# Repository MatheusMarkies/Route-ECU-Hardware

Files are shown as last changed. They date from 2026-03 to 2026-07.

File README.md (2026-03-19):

# DOCUMENTAÇÃO TÉCNICA
## Unidade de Controle Eletrônico (ECU) Automotiva

ECU-Render (https://i.ibb.co/vrg7kG9/ECU-Render.png)

---

**Versão:** 1.5  
**Data:** Setembro 2025  
**Classificação:** Documento Técnico  
**Status:** Em Desenvolvimento  

[Route ECU Firmware](https://github.com/MatheusMarkies/Route-ECU-Firmware)

---

## 1. INFORMAÇÕES GERAIS

### 1.1 Aplicação
ECU destinada ao controle de motores de combustão interna com sistema de injeção eletrônica, com capacidade para:
- 4 cilindros/injetores
- Comunicação CAN bus
- Comunicação Serial
- Armazenamento de dados e mapas

---

## 2. ESPECIFICAÇÕES TÉCNICAS

### 2.1 Especificações Elétricas

| Parâmetro | Mínimo | Típico | Máximo | Unidade |
|---|---|---|---|---|
| Tensão de Entrada | 9 | 12 | 18.81 | V |
| Corrente (Standby) | - | A Determinar | A Determinar | mA |
| Corrente (Operação) | - | A Determinar | A Determinar | mA |
| Corrente por Injetor | - | A Determinar | A Determinar | A |
| Tensão Lógica (MCU) | - | 3.3 | - | V |
| Tensão Periféricos | - | 5.0 | - | V |

Sendo a tensão de perifericos uma tensão derivada do regulador principal, porem com filtros extras para a alimentação de sensores.

### 2.2 Especificações de Gerais

| Característica | Valor | Unidade |
|---|---|---|
| Frequência MCU | 100 | MHz |
| Resolução de Tempo | A Determinar | µs |
| Taxa CAN Bus | A Determinar | kbps |
| Canais de Injeção | 4 | - |
| Canais de Ignição | 4 | - |
| Memória Flash | TBD | KB |
| Memória RAM | TBD | KB |
---

## 3. ARQUITETURA DO HARDWARE

### 3.1 Microcontrolador Principal
- **Família**: STM32H743VIT6 (ARM Cortex-M)
- **Clock Principal**: 16MHz (cristal externo) x2
- **Clock RTC**: 32.768kHz
- **Interfaces**: SPI, I2C, UART, CAN, GPIO

### 3.2 Sistema de Clock
```
Oscilador Principal (16MHz) ──▶ PLL ──▶ System Clock (100MHz)
                                  │
RTC Crystal (32.768kHz) ─────────┴──▶ RTC Clock
```

### 3.3 Mapa de Memória
- **Flash**: Código do programa
- **FRAM**: Dados grandes de acesso rapido
- **SD Card**: Log de dados e Mapas

### 3.4 Sistema de Injeção
- **Atuador**: TIP142
- **Driver**: LM1949 (Modo peak-and-hold)
- **Indicador**: LEDs indicadores individuais para cada canal de injeção

#### 3.4.2 Canais de Injeção
| Canal |
|-------|
| INJ 1 |
| INJ 2 |
| INJ 3 |
| INJ 4 |

INJECTOR (https://i.ibb.co/99wgFJhB/INJECTOR.png)

### 3.5 Sistema de Ignição
- **Atuador**: ISL9V5036P3-F085
- **Driver**: TC4424CPA (Controla duas ignições)
- **Corrente de Pico**: 3A

#### 3.5.2 Canais de Injeção
| Canal |
|------|
| IG 1 |
| IG 2 |
| IG 3 |
| IG 4 |

IGNITION (https://i.ibb.co/ycDnkN8f/IGNITION.png)

### 3.6 Sensores de Posição
- **CKP**: Posição do Virabrequim
- **CMP**: Posição do Comando de Válvulas (Se aplicavel)
- **Tipos de Entradas**: Relutância Variável e Hall
- **Condicionador de Sinal VR**: MAX9924

CKP (https://i.ibb.co/mFYfzqwf/CKP.png)

### 3.7 Sensor MAP
- **Sensor**: MPXA4250AC6U
- **Faixa de Trabalho**: 20 a 250 kPa
- **Relação de Calculo**: VOUT = VCC x (P × 0.004 – 0.04)

MAP (https://i.ibb.co/p6Ym96gr/MAP.png)

### 3.8 Sensor LAMBDA
- **Controlador**: CJ125
- **Controle de Aquecimento**: Sim
- **Sensores**: LSU4.X

LAMBDA (https://i.ibb.co/d0LBV45P/LAMBDA.png)

### 3.9 Sensores Analogicos
- **Conversor das Entradas (map)**: Tensão de Entrada no MCU = 3.205V Quando V_Sensor = 5V

#### 3.9.2 Sensores de Baixa Potencia

| Entrada | Tensão Maxima | TVS | Tipo de Entrada |
|---|---|---|---|
| Entrada 1 | 5V | Sim | Analogico |
| Entrada 2 | 5V | Sim | Analogico |
| Entrada 3 | 5V | Sim | Analogico |
| Entrada 4 | 5V | Sim | Analogico |
| Entrada 5 | 5V | Sim | Analogico |
| Entrada 6 | 5V | Sim | Analogico |
| Entrada 7 | 5V | Sim | Analogico |
| Entrada 8 | 5V | Sim | Analogico |
| Entrada 9 | 5V | Sim | Analogico |
| Entrada 10 | 5V | Sim | Analogico |
| Entrada 11 | 5V | Sim | Analogico |
| Entrada 12 | 5V | Sim | Analogico |

LOW-POWER-SENSOR (https://i.ibb.co/27B8pFJF/LOW-POWER-SENSOR.png)

#### 3.9.3 Sensores de Alta Potencia

| Entrada | Tensão Maxima | Optoacoplada | Tipo de Entrada |
|---|---|---|---|
| Entrada 1 | 12V | Sim | Analogico |
| Entrada 2 | 12V | Sim | Analogico |
| Entrada 3 | 12V | Sim | Analogico |
| Entrada 4 | 12V | Sim | Analogico |

HIGH-POWER-SENSORS (https://i.ibb.co/LzSqFQfp/HIGH-POWER-SENSORS.png)

### 3.10 Saidas

| Entrada | Tensão Maxima | PWM |
|---|---|---|
| Saida 1 | 5V | Sim |
| Saida 2 | 5V | Sim |
| Saida 3 | 5V | Sim |
| Saida 4 | 5V | Sim |

PWM (https://i.ibb.co/xtqXdg2R/PWM.png)

---

## 4. SUBSISTEMAS

### 4.1 Sistema de Alimentação

#### 4.1.1 Conversão DC-DC
- **Entrada**: 12V automotiva (9 a 18.81V)
- **Saídas**: 
  - 5V 2A (periféricos)
  - 3.3V 500mA (MCU e lógica)

## 5. INTERFACES E CONECTORES

### 5.1 Conector Principal (J1)
- **Tipo**: TE 796739-2
- **Função**: Interface principal do veículo
- **Sinais**: Alimentação, CAN, sinais de controle

### 5.2 Headers de Programação

| Designador | Tipo | Função |
|---|---|---|
| J2 | TSM-104-01-L-MT | Debug/SWD |

### 5.3 Interface SD Card (J9)
- **Conector**: 5007620483
- **Protocolo**: SPI
- **Tensão**: 3.3V
- **Capacidade**: Até 32GB

### 5.4 Pinagem do Conector Principal

| Pino | Sinal |
|-----|---|
| **A1** | INJ 1 |
| **A2** | INJ 4 |
| **A3** | INJ 3 |
| **A4** | INJ 2 |
| **B1** | Sensor_In_1 |
| **B2** | CANL |
| **B3** | CANH |
| **B4** | PWM_MCU_OUT_4  |
| **C1** | Sensor_In_2 |
| **C2** | 5V Sensor |
| **C3** | 3.3V |
| **C4** | PWM_MCU_OUT_3  |
| **D1** | Sensor_In_3 |
| **D2** | CMP_IN_1 |
| **D3** | CMP_HALL_IN |
| **D4** | PWM_MCU_OUT_2  |
| **E1** | Sensor_In_4 |
| **E2** | CMP_IN_2 |
| **E3** | GND |
| **E4** | PWM_MCU_OUT |
| **F1** | Sensor_In_5 |
| **F2** | CKP_IN |
| **F3** | CKP_HALL_IN |
| **F4** | CJ125_UP |
| **G1** | Sensor_In_6 |
| **G2** | CKP_IN_1 |
| **G3** | CJ125_IA |
| **G4** | CJ125_UA |
| **H1** | Sensor_In_7 |
| **H2** | Sensor_In_10 |
| **H3** | CJ125_US |
| **H4** | CJ125_IP |
| **J1** | Sensor_In_8 |
| **J2** | Sensor_In_11 |
| **J3** | CJ125_VM |
| **J4** | CJ125_UN |
| **K1** | Sensor_In_9 |
| **K2** | Sensor_In_12 |
| **K3** | MAP_OUT |
| **K4** | Sensor_OPT_3 |
| **L1** | Sensor_OPT_2 |
| **L2** | Sensor_OPT_1 |
| **L3** | Sensor_OPT_0 |
| **L4** | Heater OUT |
| **M1** | Ig 1 |
| **M2** | Ig 2 |
| **M3** | Ig 3 |
| **M4** | Ig 4 |

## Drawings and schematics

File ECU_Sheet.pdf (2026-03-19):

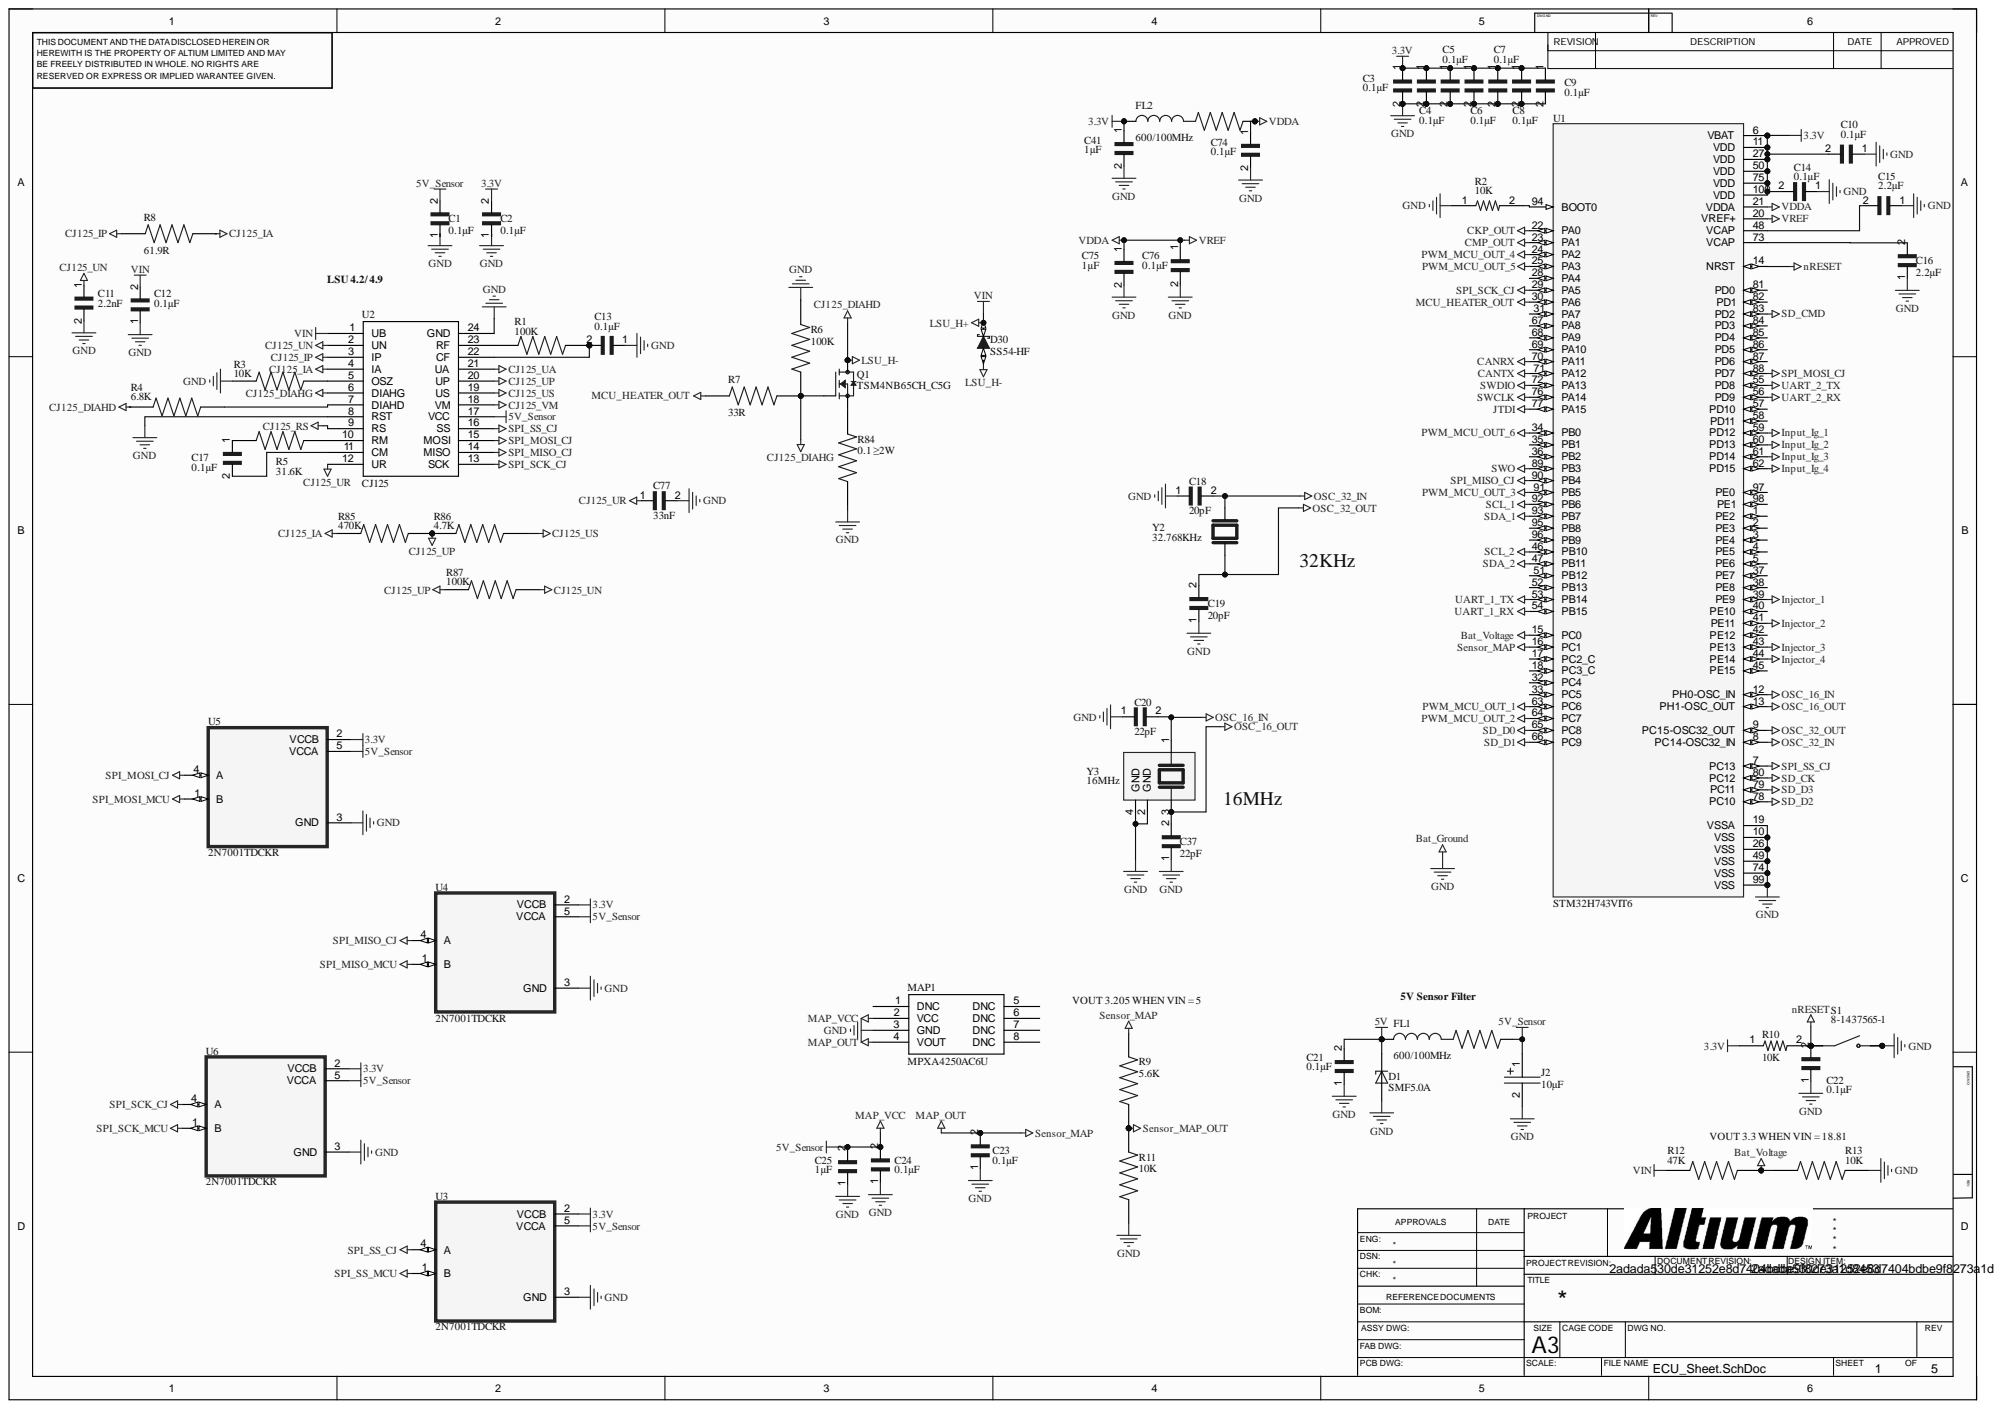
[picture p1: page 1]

1 | 2 | 3 | 4 | 5 | DWG NO: | REV: | 6

THIS DOCUMENT AND THE DATADISCLOSED HEREIN OR HEREWITH IS THE PROPERTY OF ALTIUM LIMITED AND MAY BE FREELY DISTRIBUTED IN WHOLE. NO RIGHTS ARE RESERVED OR EXPRESS OR IMPLIED WARANTEE GIVEN. | 3.3V | REVISION | DESCRIPTION | DATE | APPROVED

ENG: *
CHK: * | | TITLE *

DSN: *

PROJECTREVISION: | DOCUMENTREVISION: | DESIGN ITEM:

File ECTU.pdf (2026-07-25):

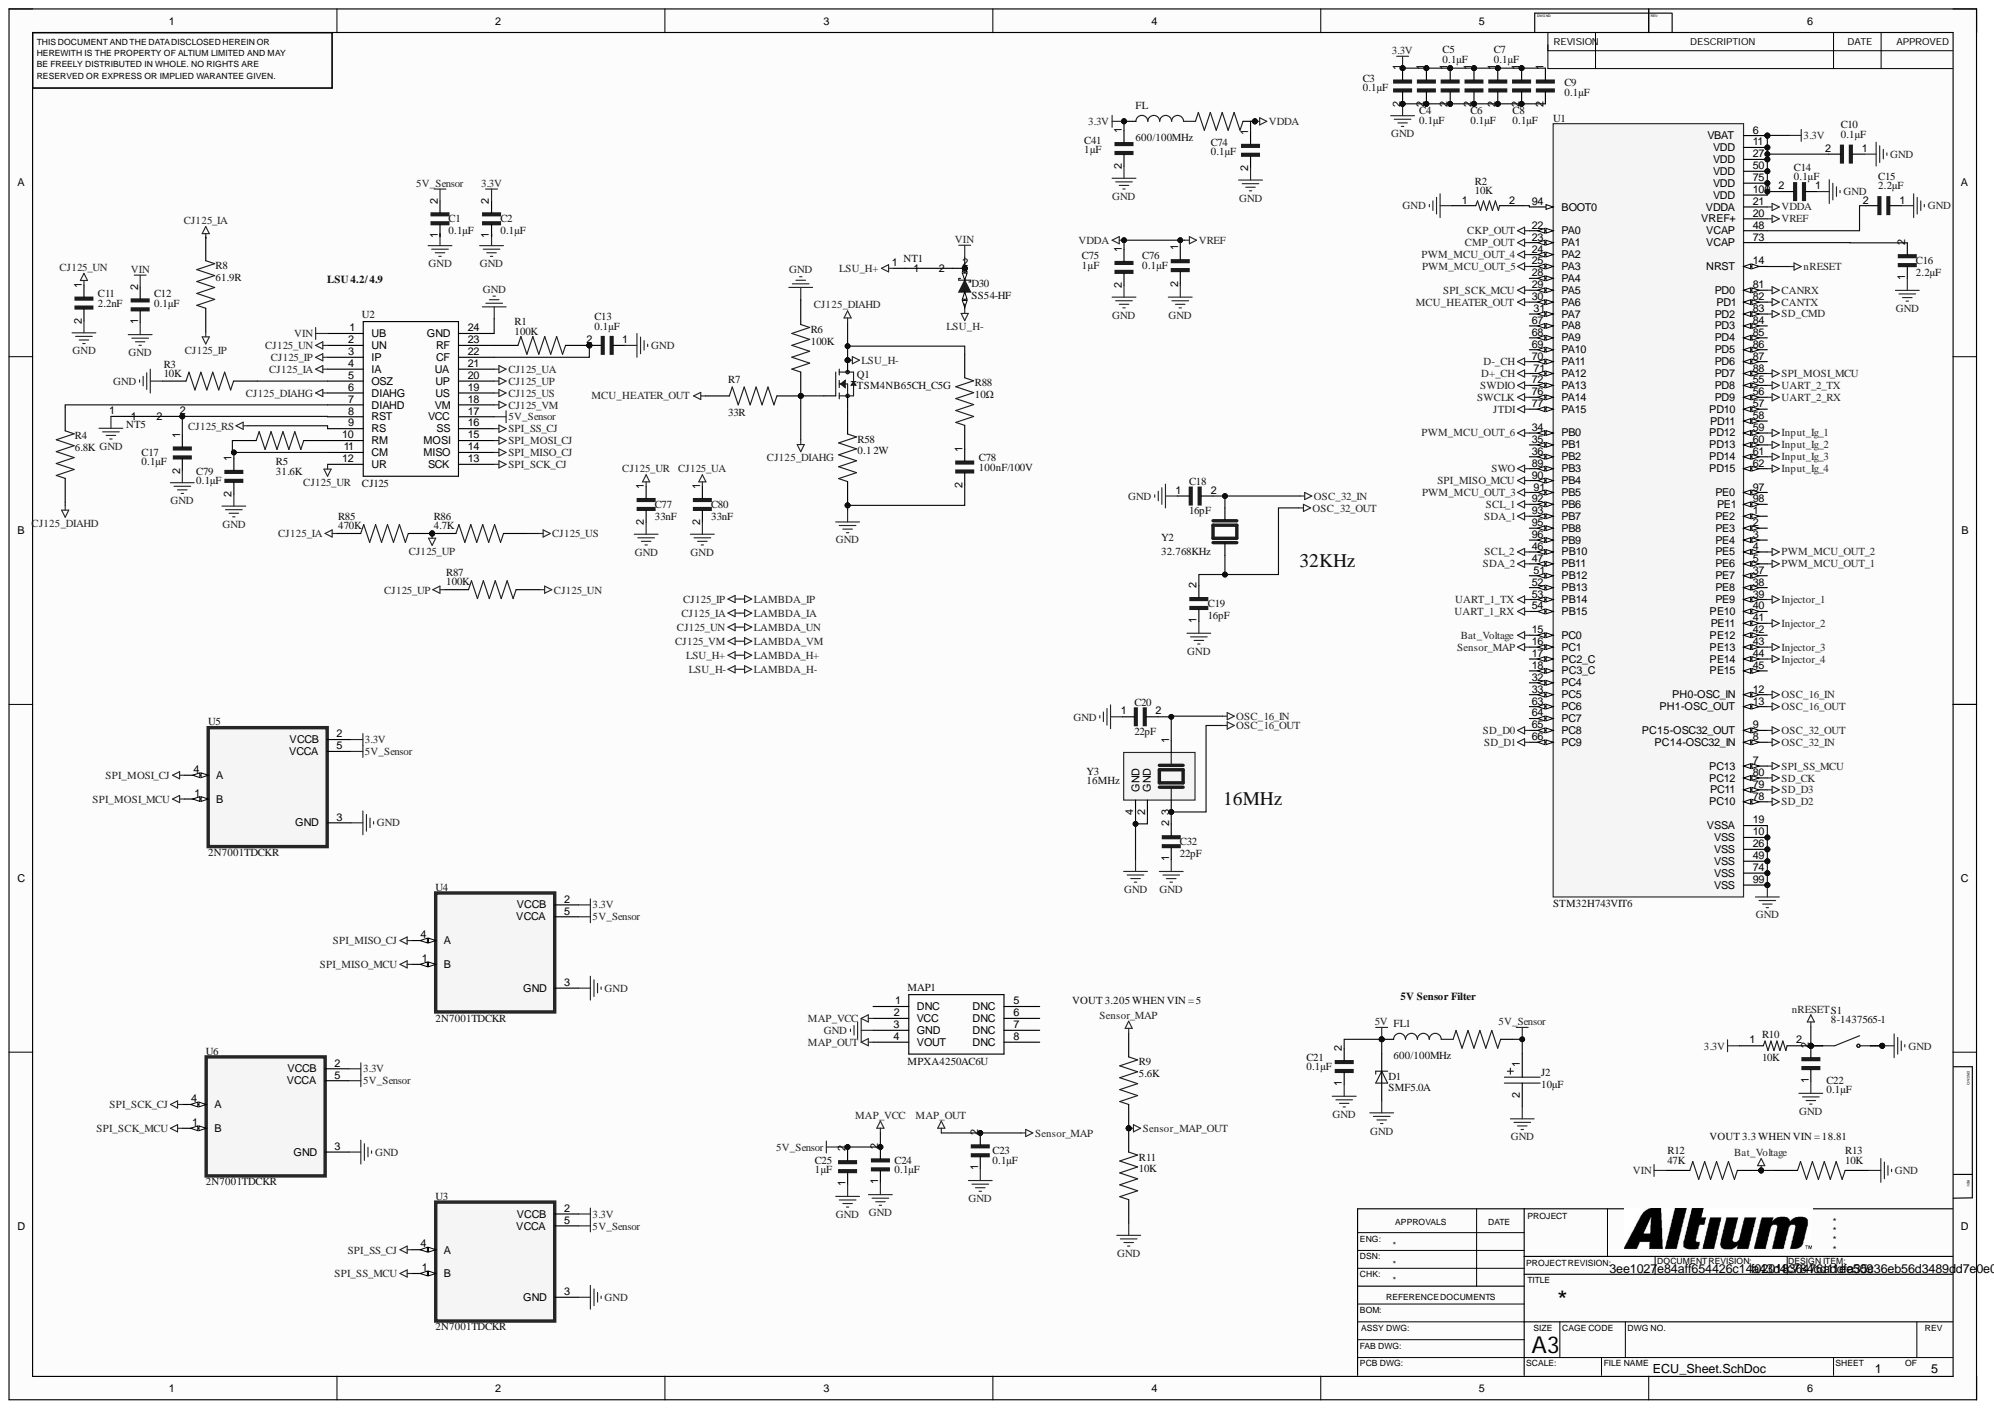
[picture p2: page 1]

DWG NO: | REV:

THIS DOCUMENT AND THE DATADISCLOSED HEREIN OR HEREWITH IS THE PROPERTY OF ALTIUM LIMITED AND MAY BE FREELY DISTRIBUTED IN WHOLE. NO RIGHTS ARE RESERVED OR EXPRESS OR IMPLIED WARANTEE GIVEN. | 3.3V | REVISION | DESCRIPTION | DATE | APPROVED

ENG: *
CHK: * | | TITLE *

DSN: *

PROJECTREVISION: | DOCUMENTREVISION: | DESIGN ITEM:

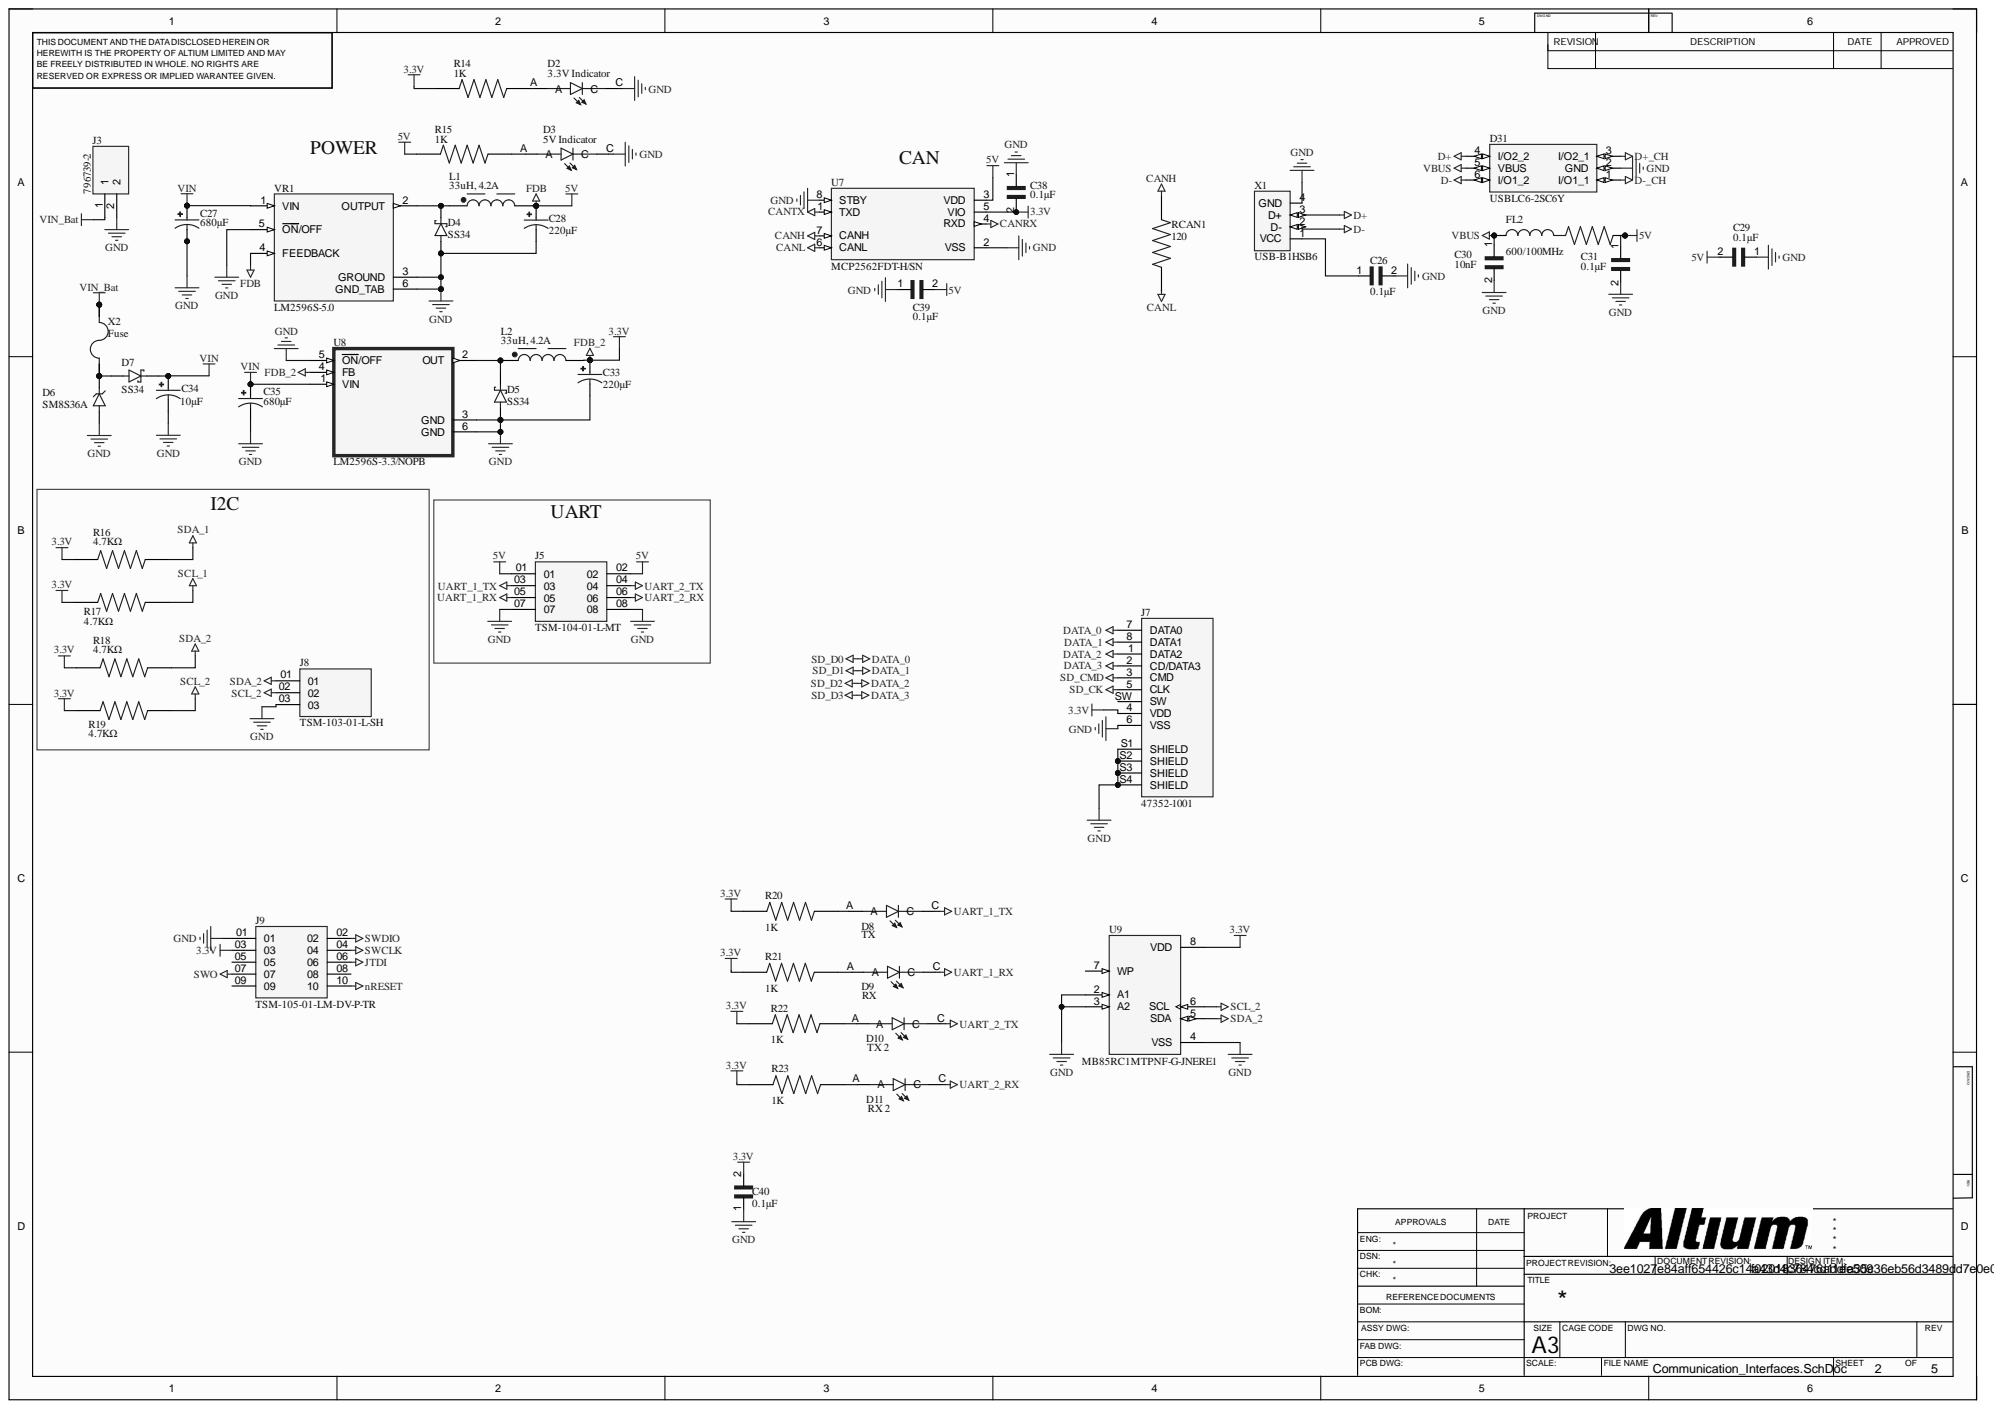
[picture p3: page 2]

TSM-105-01-LM-DV-P-TR

DSN: *

PROJECTREVISION: | DOCUMENTREVISION: | DESIGN ITEM:

CHK: * | | TITLE

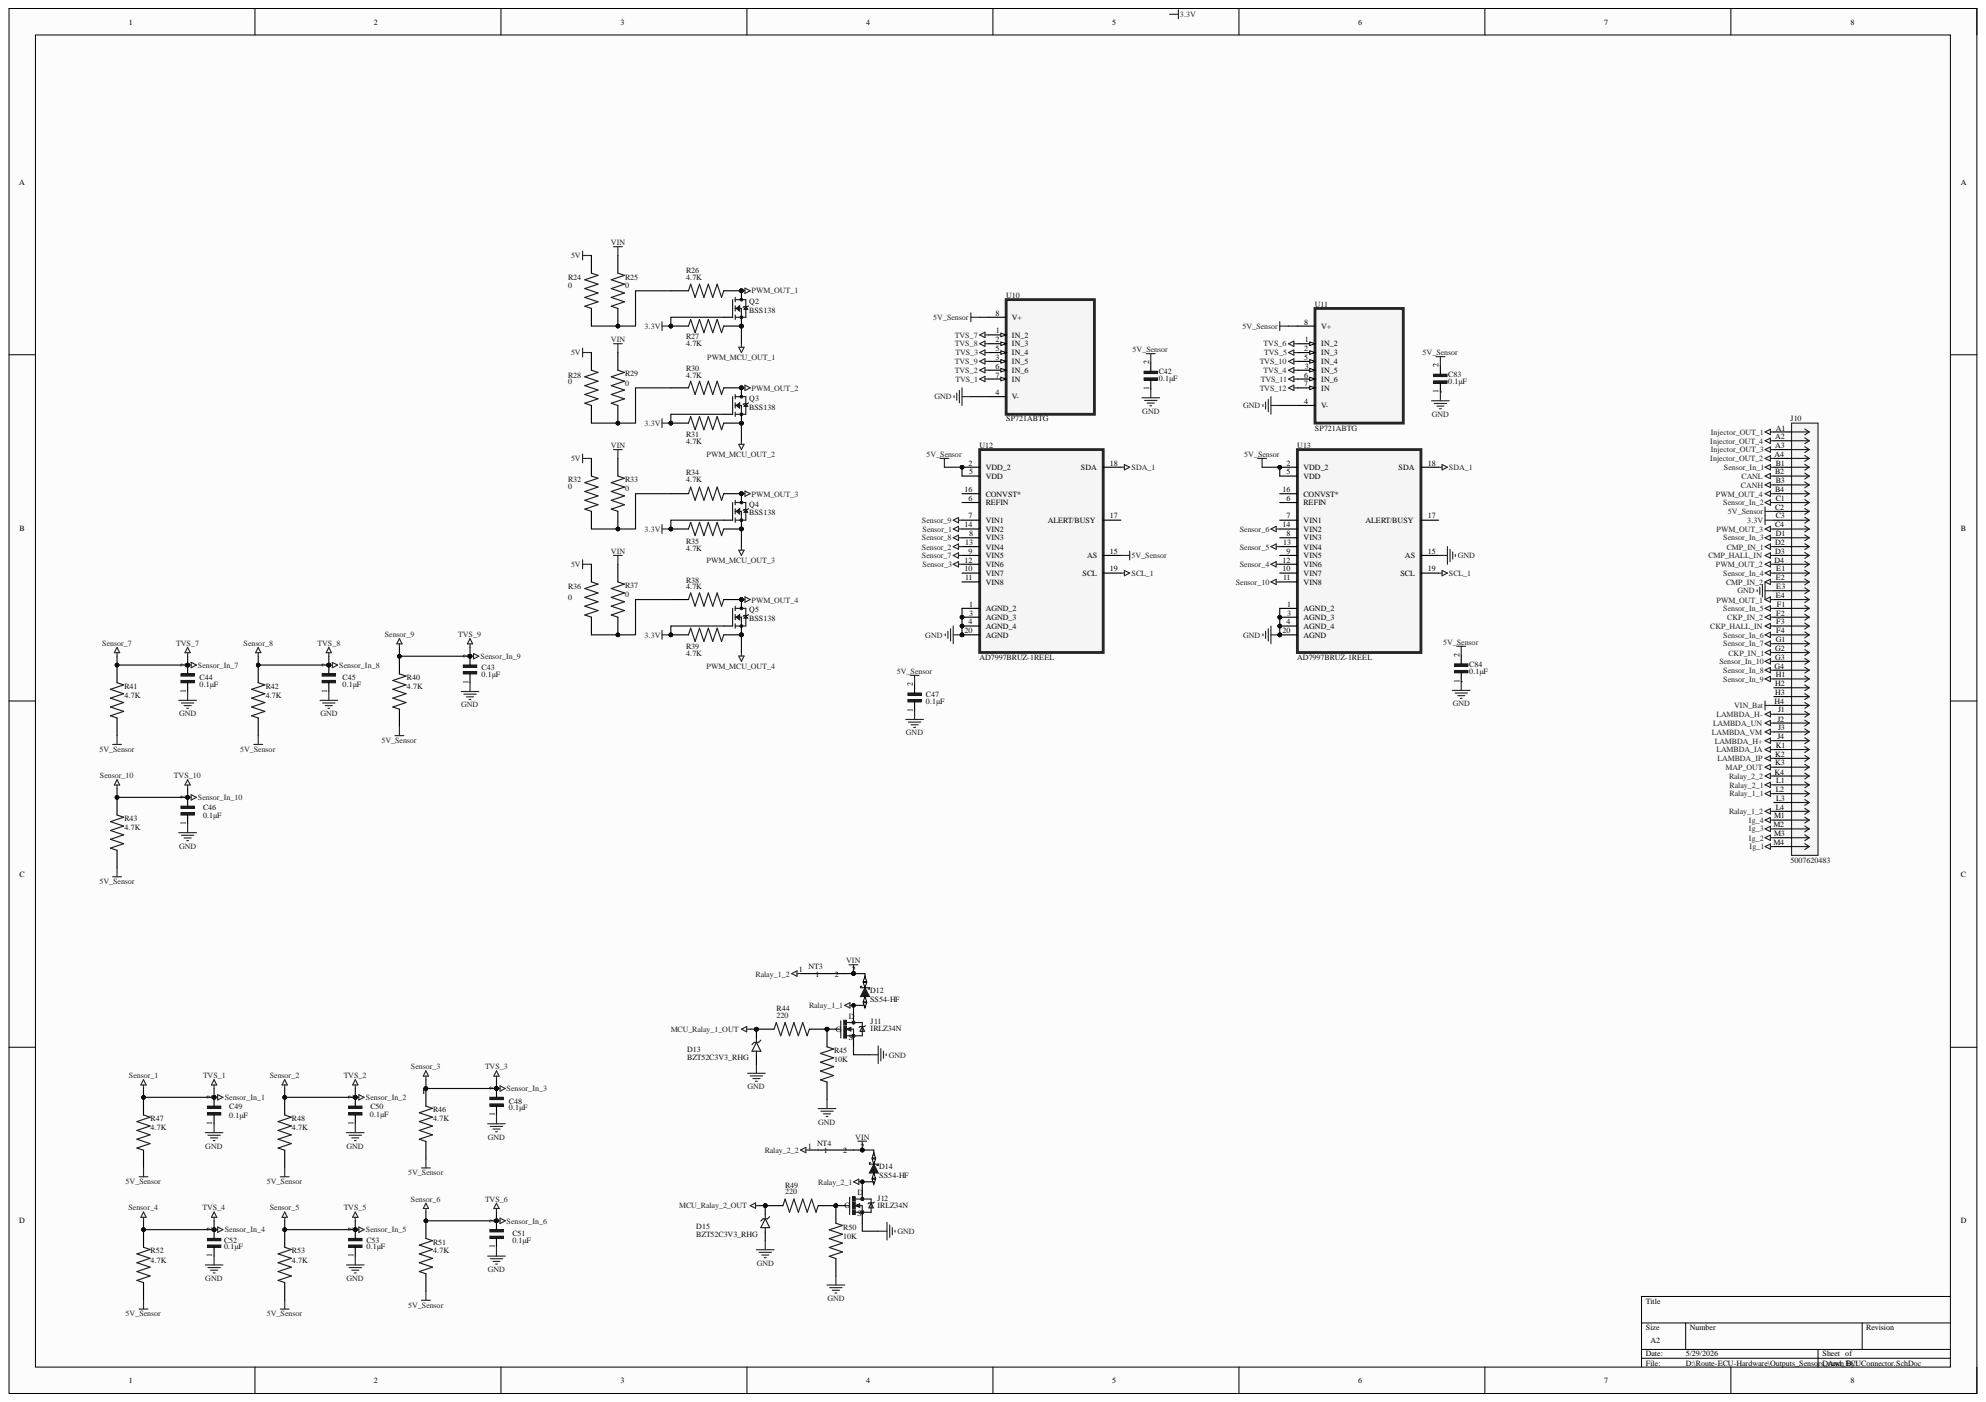
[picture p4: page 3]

sDr _And_E awn BCy:UConne

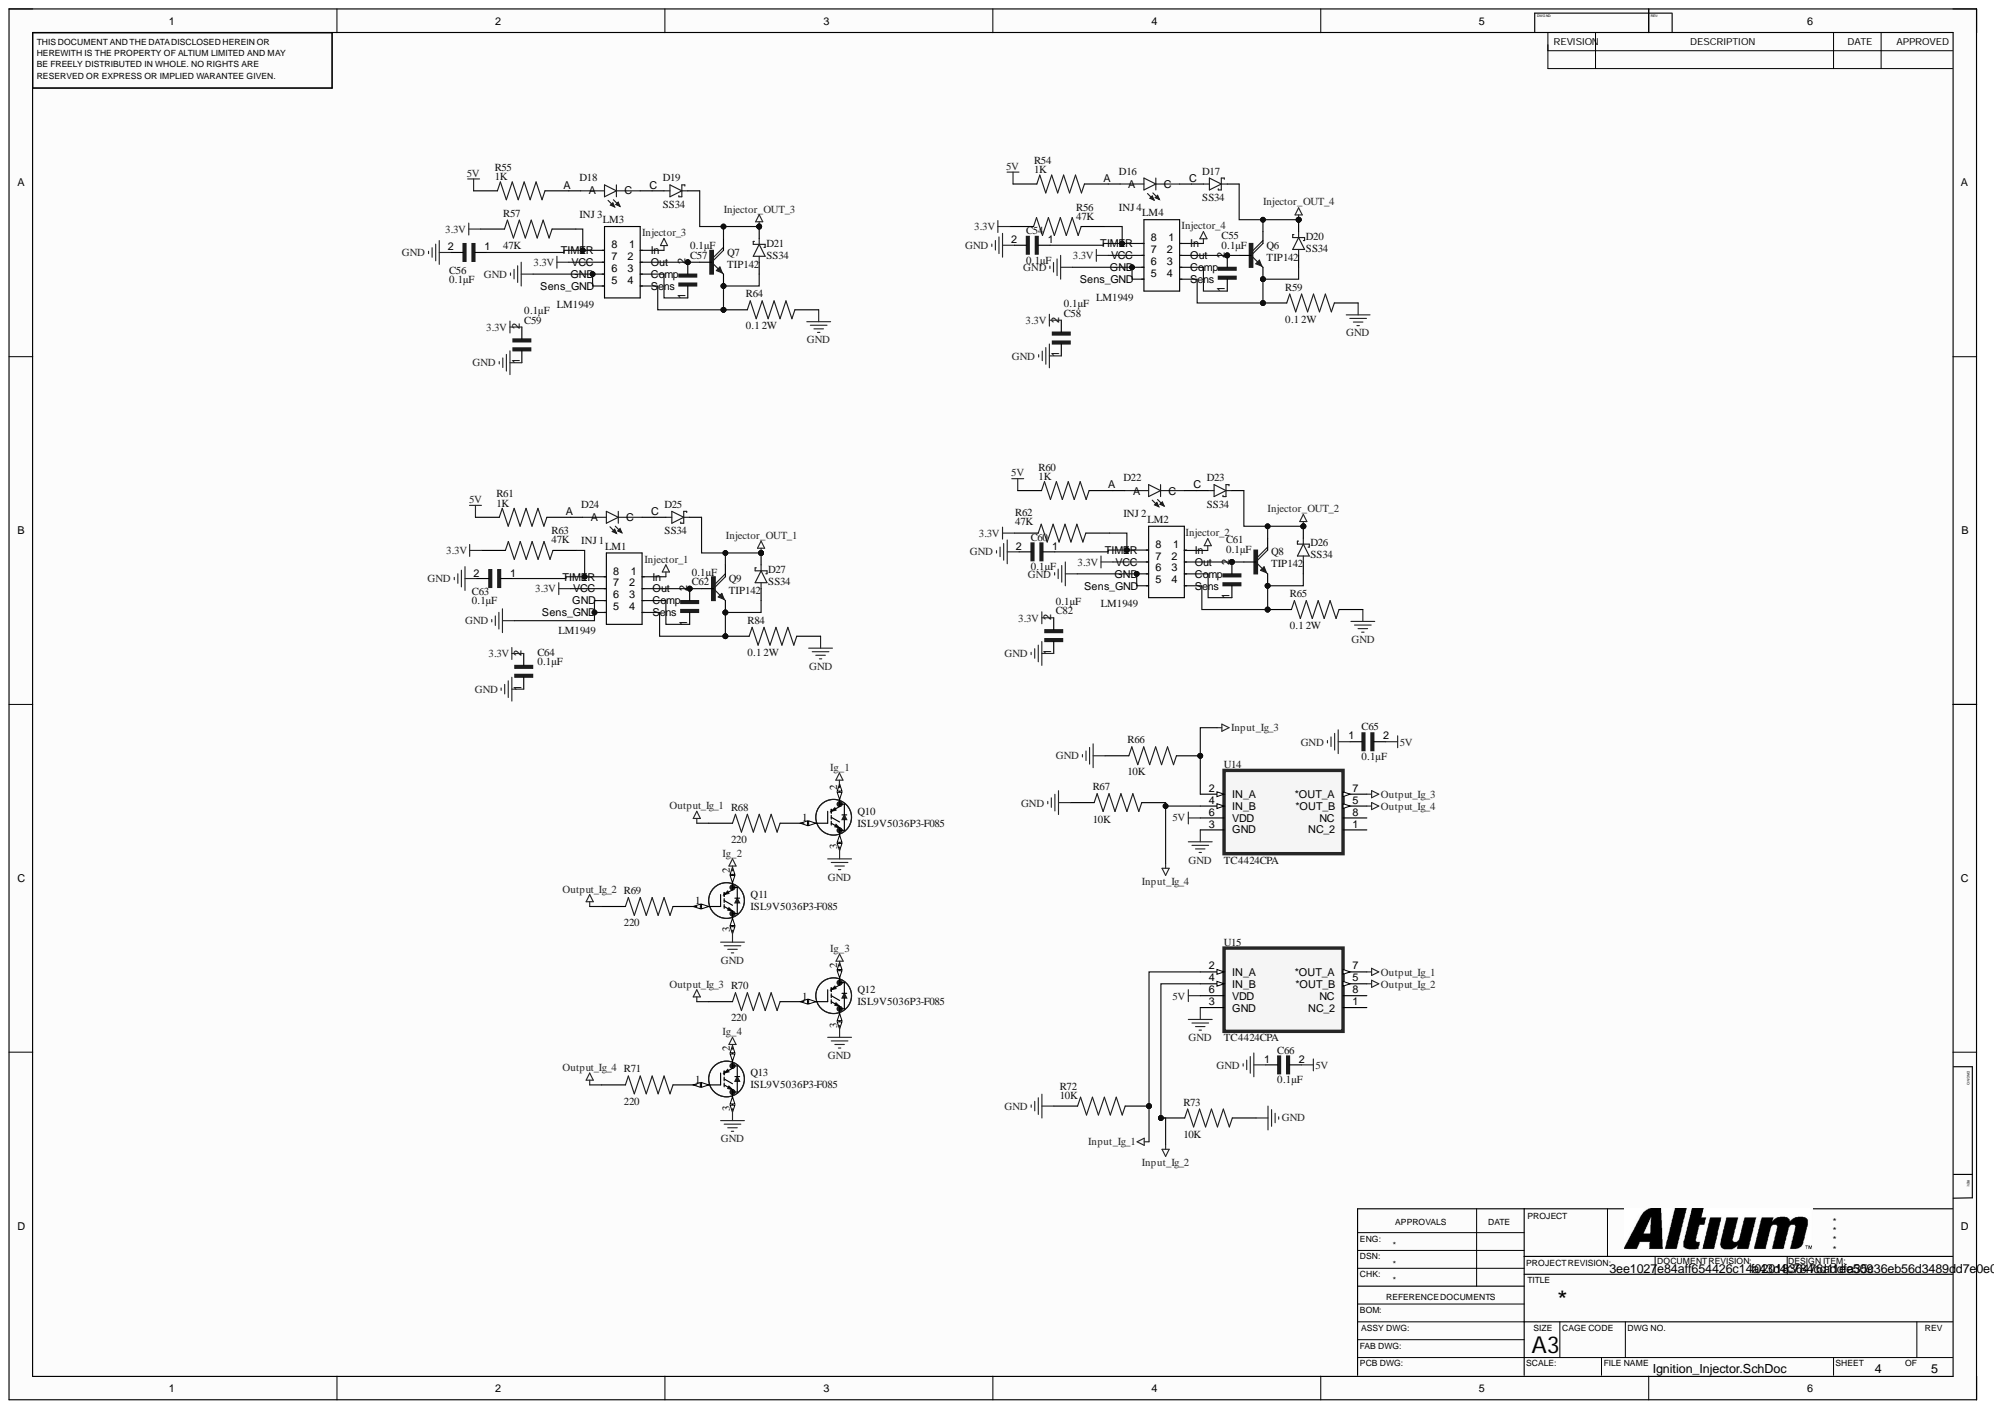
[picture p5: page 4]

Comp 3

DATE | PROJECT | * * APPROVALS * *

ENG: *

DSN: *

PROJECTREVISION: | DOCUMENTREVISION: | DESIGN ITEM:

CHK: * | | TITLE

Ignition_Injector.SchDoc | 4

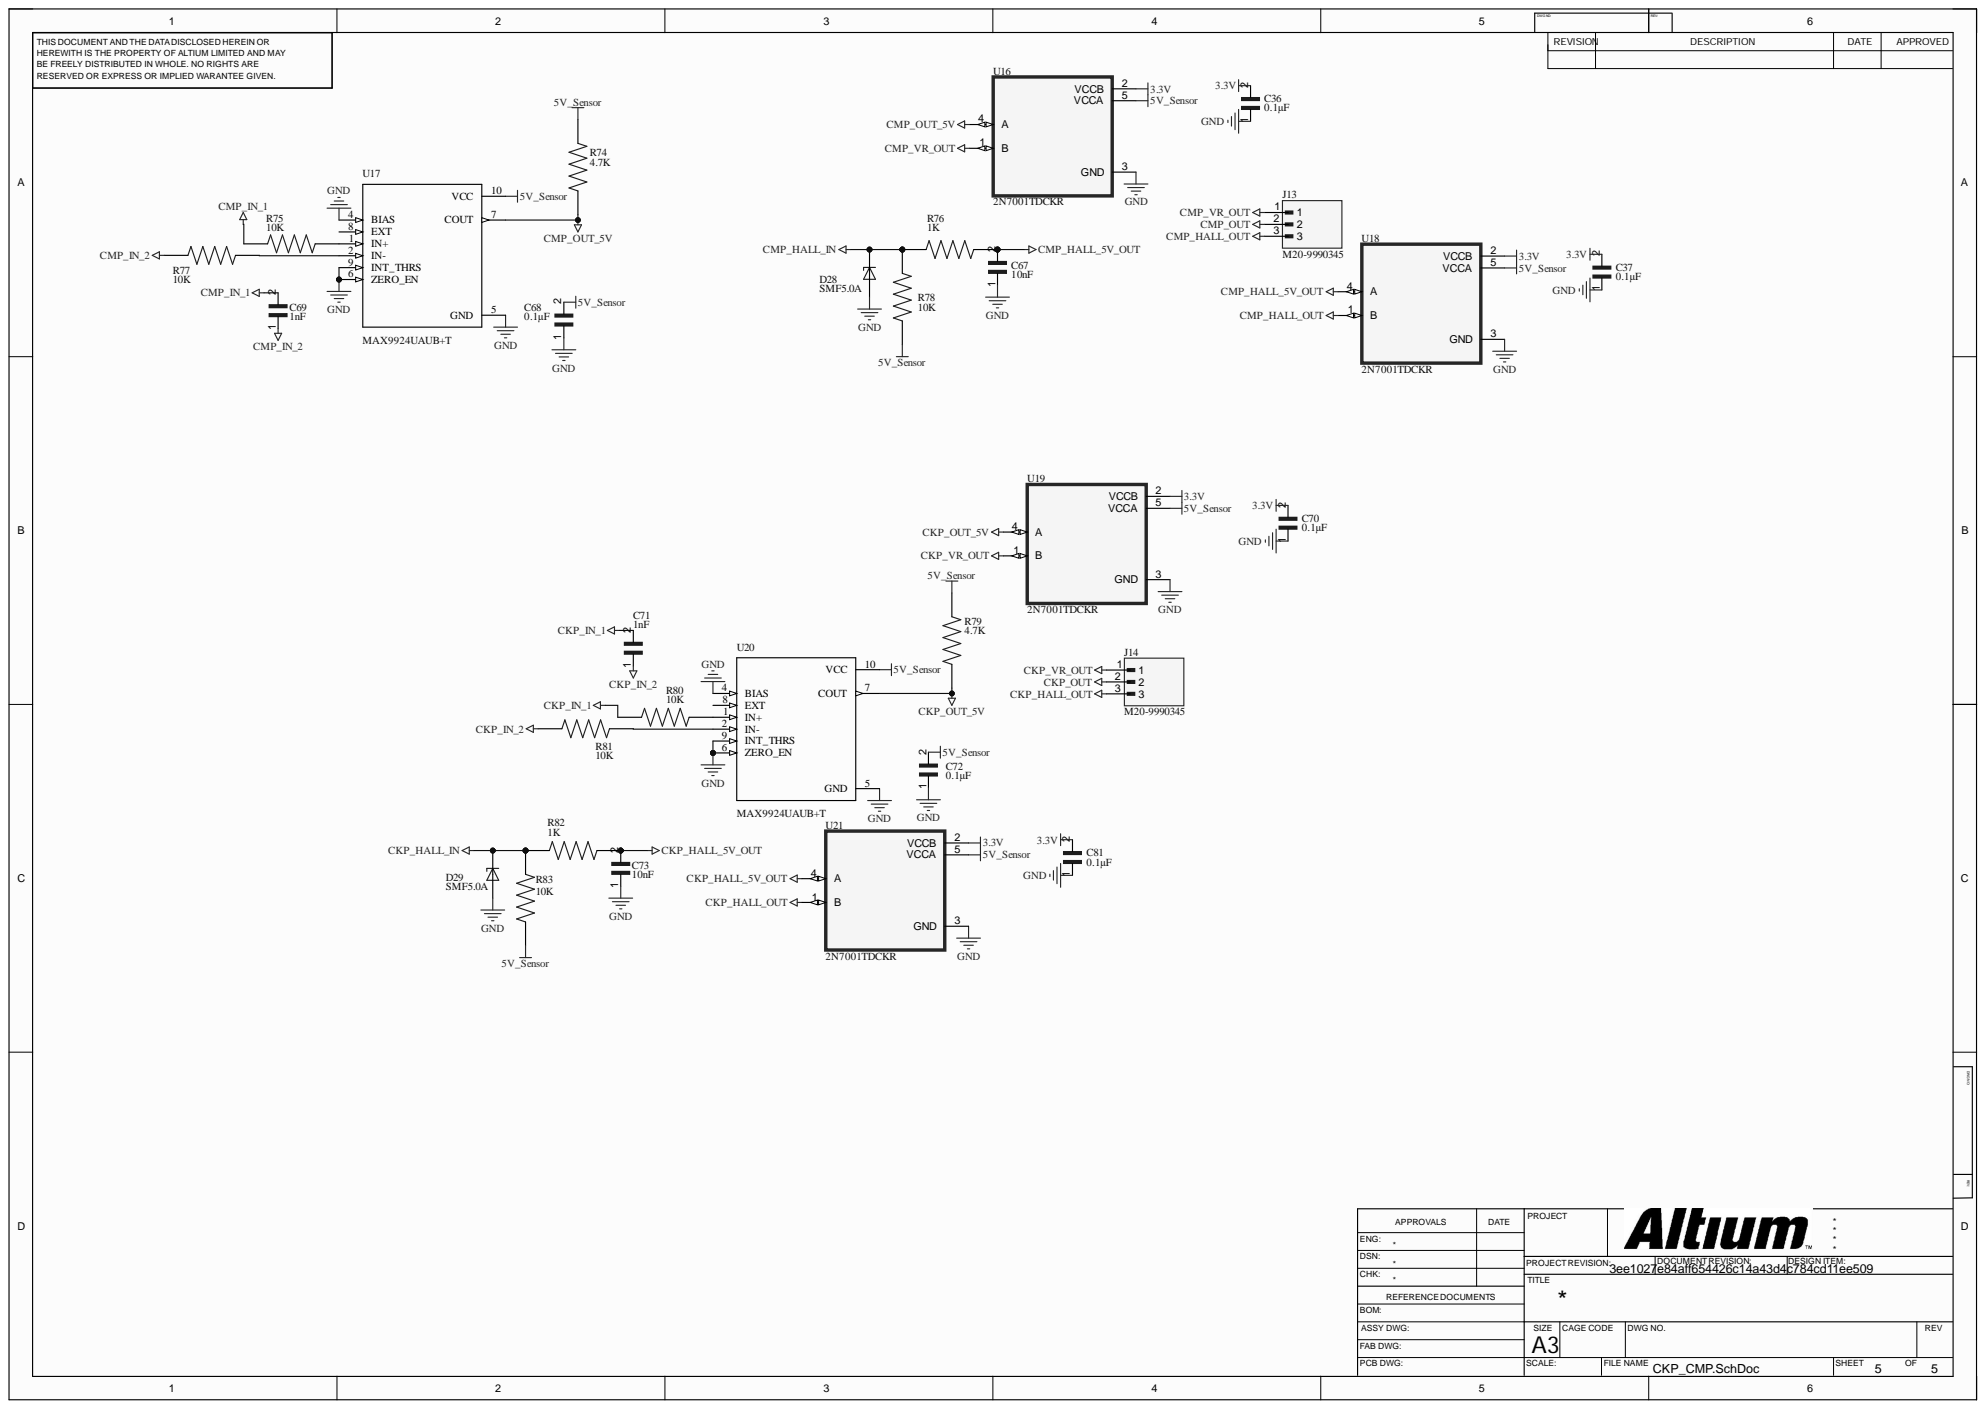
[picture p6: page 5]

DATE | PROJECT | * * APPROVALS * *

ENG: *

DSN: *

PROJECTREVISION: 3ee1027e84aff654426c14a43d4c784cd11ee509 | DOCUMENTREVISION: | DESIGN ITEM:

CHK: * | | TITLE

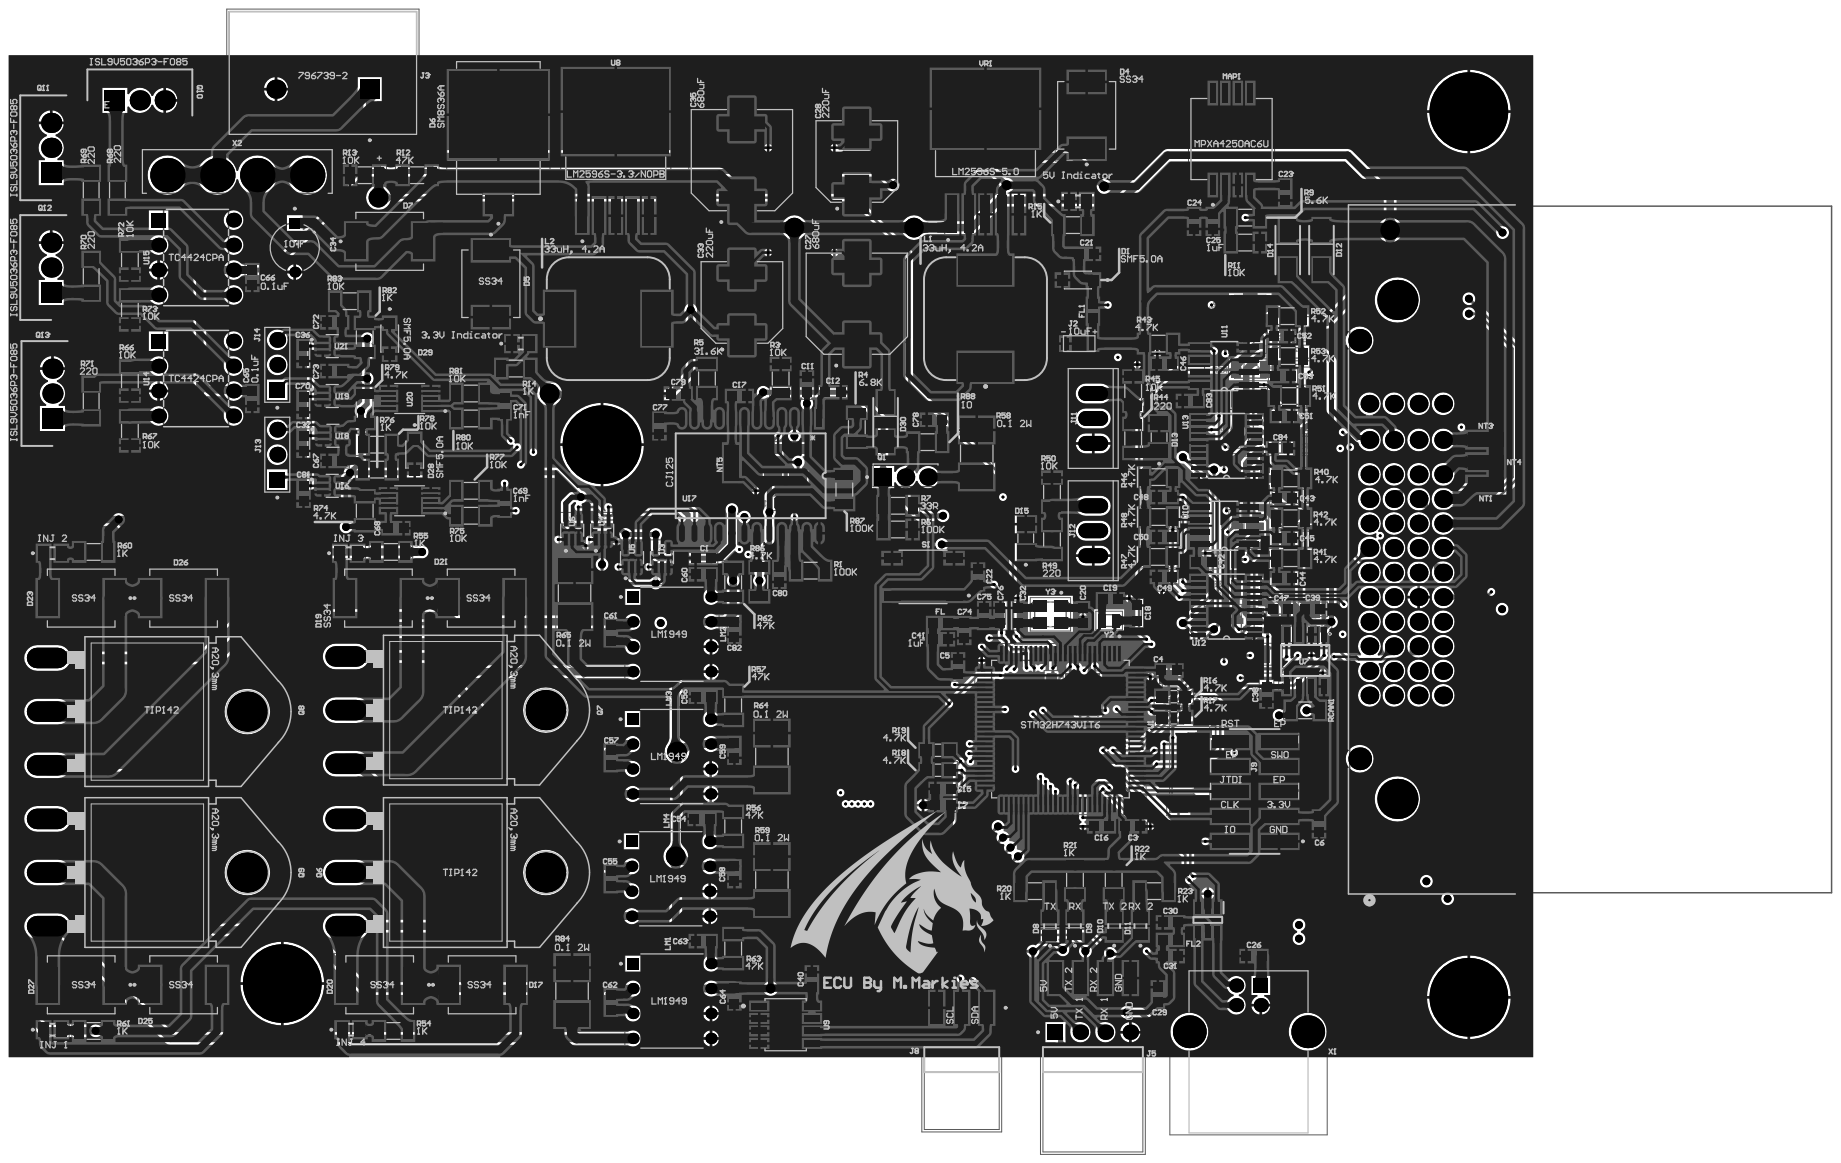
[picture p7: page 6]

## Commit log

2025-08-21 Init Commit
    [Analog_Sensors_Sheet.SchDoc, CCU_Sheet.SchDoc, DIP794W45P254L959H508Q8.PcbLib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]
2025-08-22 MCU pin remapping
    [ECTU.PrjPcb, ECTU_PCB.PcbDoc, ECU_Sheet.SchDoc]
2025-08-22 3D Bodies
    [ECTU.PrjPcb, ECTU_PCB.PcbDoc, Pick Place for ECTU_PCB.csv]
2025-08-22 Added: Gerber File
    [ECTU.PrjPcb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]
2025-10-02 Add 10-bit I2C ADC for analog sensors
    [Analog_Sensors_Sheet.SchDoc, ECTU.PrjPcb, ECTU_PCB.PcbDoc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]
2025-10-26 Add additional PWM outputs
    [Analog_Sensors_Sheet.SchDoc, CCU_Sheet.SchDoc, ECTU.PrjPcb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]
2026-02-03 CKP and CMP
    [CCU_Sheet.SchDoc, ECTU.PrjPcb, ECTU_PCB.PcbDoc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]
2026-02-13 Added: Extra protection at battery input, relay activation system. Removed: Optocoupled sensors and pull-down sensors.
    [Analog_Sensors_Sheet.SchDoc, CCU_Sheet.SchDoc]
2026-02-13 Component names have been reset
    [Analog_Sensors_Sheet.SchDoc, CCU_Sheet.SchDoc, CKP_CMP.SchDoc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]
2026-03-18 CAN Updates
    [CKP_CMP.SchDoc, ECTU_PCB.PcbDoc, ECU_Sheet.SchDoc]
2026-03-18 Rename Files
    [Analog_Sensors_Sheet.SchDoc, CCU_Sheet.SchDoc, Communication_Interfaces.SchDoc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]
2026-03-18 Rename Components
    [Communication_Interfaces.SchDoc, ECU_Sheet.SchDoc]
2026-03-19 Lambda Updates
    [ECTU.PrjPcb, ECU_Sheet.SchDoc, Ignition_Injector.SchDoc]
2026-03-19 Shunt Resistor 0.1 2W 2512
    [ECU_Sheet.SchDoc, Ignition_Injector.SchDoc]
2026-03-19 Main Connector Updates
    [ECTU.PrjPcb, ECU_Sheet.SchDoc, Outputs_Sensors_And_ECUConnector.SchDoc]
2026-03-26 USB OTG
    [CKP_CMP.SchDoc, Communication_Interfaces.SchDoc, ECTU.PrjPcb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]
2026-03-30 Added: Net Ties
    [CKP_CMP.SchDoc, ECTU.PrjPcb, ECTU_PCB.PcbDoc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]
2026-03-30 PCB Layout Update
    [ECTU_PCB.PcbDoc, Ignition_Injector.SchDoc]
2026-05-13 Traced PCB
    [Communication_Interfaces.SchDoc, ECTU_PCB.PcbDoc, ECU_Sheet.SchDoc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]
